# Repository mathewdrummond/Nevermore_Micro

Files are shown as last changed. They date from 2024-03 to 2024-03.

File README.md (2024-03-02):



# Nevermore Activated Carbon Filters - Micro Edition

<div align="center">Nevermore Micro V5 Duo (dual fan)</div>

Nevermore Activated Carbon Filter Micro V5 Duo

<div align="center">Nevermore Micro V4 (single fan)</div>

Nevermore Activated Carbon Filter Micro V4

Originally intended as a carbon fume filter for Voron V2, it has found its way into a multitude of other machines. Let yours be the next! Bad smells or fumes, or complaints thereof, should not keep you from being a maker!

- [Nevermore Activated Carbon Filters - Micro Edition](#nevermore-activated-carbon-filters---micro-edition)
- [About The Nevermore Micro](#about-the-nevermore-micro)
  - [Why The Nevermore?](#why-the-nevermore)
  - [Nevermore Background](#nevermore-background)
  - [Nevermore V4, First Release](#nevermore-v4-first-release)
  - [Nevermore V5 Duo](#nevermore-v5-duo)
- [FAQs](#faqs)
  - [What are differences between V4 and V5 Duo?](#what-are-differences-between-v4-and-v5-duo)
  - [Why use a single fan version, if dual is better?](#why-use-a-single-fan-version-if-dual-is-better)
  - [What other changes does V5 bring?](#what-other-changes-does-v5-bring)
  - [What fans should I use?](#what-fans-should-i-use)
  - [How do I make a suggestion/report a bug/find out more?](#how-do-i-make-a-suggestionreport-a-bugfind-out-more)
- [Getting Started](#getting-started)
  - [SOURCING THE PROPER ACID-FREE CARBON](#sourcing-the-proper-acid-free-carbon)
  - [NEVERMORE 3D PRINTER CARBON](#nevermore-3d-printer-carbon)
  - [BOM (V5)](#bom-v5)
  - [BOM (V4)](#bom-v4)
  - [Assembly](#assembly)
    - [Instructions for V5](#instructions-for-v5)
    - [Instructions for V4](#instructions-for-v4)
  - [Final Thoughts on Usage](#final-thoughts-on-usage)
- [Credits](#credits)
  - [Contributing](#contributing)
  - [License](#license)
  - [Contact](#contact)
  - [Acknowledgements](#acknowledgements)
  - [Special Thanks](#special-thanks)

# About The Nevermore Micro

[VOCs (Volatile Organic Compounds)](https://en.wikipedia.org/wiki/Volatile_organic_compound) are common in daily life but VOCs generated from 3D printing are known to cause severe health issues and even cause cancer in some cases.

Emitted VOCs

A study from 2013 of [ultrafine particle emissions from desktop 3D printers (2013)](https://www.sciencedirect.com/science/article/pii/S1352231013005086) is a good start to understand the importance of your filament choices and the printer's environment.

Characterization of volatile organic compound emissions from consumer level material extrusion 3D printers (2019)
_(credit: [Characterization of volatile organic compound emissions from consumer level material extrusion 3D printers (2019)](https://www.sciencedirect.com/science/article/pii/S0360132319304196))_

Characterization of particulate and gaseous pollutants emitted during operation of a desktop 3D printer (2019)
_(credit: [Characterization of particulate and gaseous pollutants emitted during operation of a desktop 3D printer (2019)](https://www.sciencedirect.com/science/article/pii/S0160412018323663))_

## Why The Nevermore?

At the end of the day, a fresh single-pass filtered exhaust (at brand new) has perhaps 70% VOC removal efficiency while still exhausting 30% of the nasty. A worn-in 50% efficiency recirculation filter achieving four passes would still remove 94% of the bad stuff. Or 99% at six passes!

The number of passes you get all depends on how well you can seal your build chamber.

Some will have a hard time achieving a good chamber seal, which creates the biggest drawback of recirculation filters - _they're air flow neutral_. Meaning, as nothing pulls air into the chamber, air can diffuse freely to the outside through any remaining gaps. And that air could be _zero-per-cent_ cleaned...

If you plan on using only a Nevermore - be sure to seal your chamber as good as possible to prevent diffusing.

## Nevermore Background

There are many options for 3d printing air filters. Here’s a short list, and why I eventually settled on creating Nevermore:

**1. Home air purifiers**

**PRO:** Plug and play! High air flow (mostly). Will filter most particles a 3d printer produces.

**CON:** ABS headaches are not from particles, but Volatile Organic Compounds (VOCs), that are two orders of magnitude smaller than any particles a HEPA or ULPA could trap - they’re essentially gasses.

While home purifiers typically also contains carbon filtration and/or photocatlytic UV filtration stages, they will still not be suitable for 3d printing. Why? Efficient carbon adsorption in sufficient amount and stages is an absolute airflow killer, so most purifiers contain only a thin layer of carbon mesh/pellets that will be fully adsorbed within days or weeks at full power. And even if the filter is not used, contact with air saturates the carbon in 1-2 months. Yet they’re advertised as lasting for 6 months – that's only true for the HEPA component, not the VOC adsorbant carbon we're after.

And replacement filters typically run 20-60 USD a pop. Quite a lot for changing every few weeks when the carbon component depletes.

UV photocatalyst activity can last though; however, breakdown is slow and inefficient with voc halflives of several hours. The TiO2 layer reacting to the UV will also easily get irreversibly blocked by silicates (of which there are a lot in peoples homes, in everything from sink and bathroom sealants to plaster walls). And breakdown will many times be incomplete. Styrene passing a PCO filter might get turned to even more dangerous benzene, for instance.

**2. Carbon/HEPA filter combinations like the Zortrax M Series HEPA Filters**

Same as above. The HEPA component will keep working, but the carbon is just a few pebbles per hex. It could provide partial VOC clearance when fresh, but will quickly deplete with air flow. Then you need to replace it for 36 USD after a week of printing.

**3. Wet scrubber**

Awesome for both particles and VOCs, but its an industrial solution with any smaller home versions plagued by loud noise, water leakage and mechanical issues. It's not a solution for the masses.

**So, how about Nevermore?**

Well, the carbon in those filters mentioned above, costing a lot for little duration is actually dirt cheap. Whereas you get 20 grams for 36 USD with a zortax filter, **you can get 5000 grams for 36 USD in bulk**.

And with an enclosed chamber, you don't need the air flow of a room-size air purifier. Even a 350mm V2 Voron only holds about 5cf, meaning even a partial flow from a 5015 fan of 0.5-2cfm is enough to filter the fumes efficiently at the source.

So what are we waiting for? We got lots of cheap carbon. We can replace it easily. We don't need high airflow to clean a small chamber. We deal with poor efficiency of one-pass carbon filters by multiplying the amount and recirculate the air.

Enter, _The Nevermore_.

## Nevermore V4, First Release

Nevermore V4 is a refinement of the V3. V4 adds a air guides, as the previous versions had the majority of air flow on just one side of the filter (most recent version has all supports removed yet again!). The cartridge lid also mounts a bit sturdier, and V4 now has separate base pieces for use with Vorons other than 2.4.

Nevermore Micro V2 Prototype

The V4 was the first official release of the Nevermore Micro to the public.

## Nevermore V5 Duo

Following the V4, the V5 Duo was released that changes the direction of air flow, better suited for when the Nevermore Micro would be placed flat on the bottom or top of the printer. Though there are other "outlet" options, like for the V1.8/Trident style that blows outwards and not up.

The V5 Duo also adds a 2nd additional 5015.

Nevermore Micro V5 Duo

Nevermore Micro V5 Duo

_(Nevermore V5 Duo. used with permission from Tightwad(JT)#6055)_

This repository hosts both versions, as they are the same in design and function.

# FAQs

## What are differences between V4 and V5 Duo?

The current NM Micro versions are V4 and V5 Duo.

V4 utilizes a single dissected 5015 fan that is glued in place to spread the airflow over the entire filter surface (something impossible to do with an intact scroll, which focuses the air too much). The intake is on the top, and exhausts out the front.

V5 Duo uses two blowers in parallel to achieve a more even spread of airflow while keeping the pressure-generating scrolls intact; however, it still needs some slight modifications to the scroll exhaust. The intake is on the top, and exhausts upwards.

## Why use a single fan version, if dual is better?

_Dual is not better._ The area per blower is halved, so what is gained in air flow is lost in increased restriction per blower. There should be some improvements though, from linear air flow and intact scroll.

Also, the V4 single fan version may be better suited for printers where the Micro has to be mounted vertically, like on the side of a Voron V0.

Voron V0.1 with Nevermore V4

_(Voron V0.1 w/Nevermore V4. used with permission from DoubleT#0448)_

The single fan version of the V4 design in the Voron V0 above would draw the air from under the build plate, and exhaust it upwards, creating a circulation flow within the printer.

Air circulation is critical to filter as much of the VOCs within the build chamber as possible. Not only that, but it would help heat the chamber faster and achieve higher chamber temps.

However, on a Voron V2 or similar printer, the V5 Duo version would be better suited when placed under the bed as the upward exhaust venting creates a good circulation effect.



_(Voron V2 w/Nevermore V5. used with permission from Laserbeak43#2729)_

## What other changes does V5 bring?

- Exhausts air upwards
  - Better heat spread in the Voron V2 chamber
  - Less air leaks through Voron V2 split doors
- BOM 6x3 magnets are standard
- Blower fans are seated by bolts again, with less modifications needed

## What fans should I use?

Aim for any 5015 blower with a rating above 200Pa / 20mmH2O / 1 inH2O.

Since the fan (probably) cant be reused for other projects and will function in a high temp environment affecting its lifetime, go for budget. The Sunon Maglev MF50151VX (12V) / MF50152VX (24V) (high speed version, 6000 rpm) is good but unfortunately almost impossible to find as most are fakes. The GDStime 6000rpm Dual Ball bearing is another good option, but quality may vary. The Delta BFB0524HH is a gucci option, as is the special micro versions made for the papst rlf-35 which is an equally awesome and expensive fan. Any fan that works well for stealthburner should be a good option for nevermore micro as well.

See the BOM below for more details.

## How do I make a suggestion/report a bug/find out more?

- [The Nevermore Micro](https://github.com/nevermore3d/Nevermore_Micro)
  - [Report a Bug](https://github.com/nevermore3d/Nevermore_Micro/issues)
  - [Request a Feature](https://github.com/nevermore3d/Nevermore_Micro/issues)
- [Explore all Nevermore Activated Carbon Filters](https://github.com/nevermore3d)

# Getting Started

You're ready to build a Nevermore Micro? Cool!

> [!NOTE]  
> MADE FOR ABS/PC/PETG - USE A DECENTLY HEAT RESISTANT FILAMENT !!

> [!NOTE]  
>  Since you are committing to fan dissection, be aware a 5015 used for a NM Micro will most likely never find a different purpose!

## SOURCING THE PROPER ACID-FREE CARBON

**IMPORTANT!** Since first release the varying quality carbon out there has become increasingly evident. Users has both gotten bad carbon as well as outright dangerous stuff (in one case oxidizing most metal surfaces in a new voron in minutes. Be sure to vet your carbon supplier! You do not want your printer to look like this.

Acid residue on end-stop switch oxidizing

_(z end-stop switch after using acid residue carbon for 30 minutes, oxidizing)_

Acid residue on rails and screws oxidizing

_(oxidation on rails and screws after using acid residue carbon. used with permission from Zeptron#8880)_

Acid residue on filament tension spring oxidizing

_(oxidation on filament tension spring after using acid residue carbon. used with permission from Zeptron#8880)_

Acid residue on bolts and washers oxidizing

_(oxidation on bolts and washers after using acid residue carbon. used with permission from Zeptron#8880)_

Optimal carbon for 3D printer VOC adsorption is sourced from **virgin coconut**, not wood/bitumen/charcoal/bamboo/lignin/etc. The porosity for each and every source will vary greatly.

For example, for aquarium or moonshine use you want large macroporosity to filter larger impurities, like oils. For that reason, water/liquid-use carbon has a large macropore area, defined as >100nm. 3D Printer VOCs are generally less than 0.5 nm, meaning that **for optimal capture rate and efficiency we want carbon with a high microporosity ratio, defined as <1nm**. A higher iodine count >1000 usually indicates at least some micro/mesoporosity, and a higher hardness (>95%) will create less dust in air filtration. CTC number doesn't translate well to our VOCs; however, toluene adsorption - which sometimes is available - is a good metric.

**Avoid acid washed carbon at all costs**. Residues have oxidized printers! Go for steam activated, non acid-washed. A blend of neutral carbon and alkaline KOH carbon might be the best blend in the future, but impossible to currently source from trustworthy manufacturers.

Finding carbon that fills all criteria is hard. Look around, ask suppliers about the carbon, hear what others recommend. 

## NEVERMORE 3D PRINTER CARBON
**Nevermore offers its own premium carbon of unmatched specifications through selected voron resellers.** Its the best activated carbon for 3D printer use we have found after speaking to most major, vetted suppliers, offering benzene adsorbtion of up to 48 wt%, surface area of 1250 and CTC value of 80. It doesn't come cheap compared to bulk carbon from amazon, but its safe, has unbeatable performance, and every purchase supports the nevermore project by at least a dollar.  

[All Nevermore resellers here](https://github.com/nevermore3d/Reseller)

## BOM (V5)

- 2x 5015 blowers (rating above 200Pa / 20mmH2O / 1 inH2O)
  - Sunon Maglev MF5015VX (high speed version, 6000 rpm. NOTE: There are A LOT of fake sunons out there, even from usually reputable sources. Blantant examples include 24V versions. Also, Sunon does not officially reecommend PWM:ing this fan, so while its still perfectly doable it can have unintended consequences later on) (There is no 24V version for this fan only comes in 12 V)
  - GDStime 6000rpm Dual Ball bearing on Aliexpress (This is 12V rated fans)
  - Delta BFB0524HH (This is 24V rated fans)
  - Avoid mechatronics fans for this purpose.
- 6x M3, 5 mm OD, 4 mm height heatset inserts (standard voron issue)
  - 1 in plenum base to secure plenum lid
  - 1 in cartridge base to secure cartridge lide
  - 4 in fans (2 in each fan × 2 fans)
- 8x ⌀6x3 mm round magnets
- 1x 2 pin JST header
- 4x M3x16 BHCS
  - for heat inserts that go into the four fan tabs
- 1x M3x18 BHCS
  - ONLY for delta and v1.8 variants
- 1x M3x6 BHCS
- 1x M3x4 BHCS
  - for the extra hole in the plenum@lid for symmetry (it doesn’t attach to anything and is totally optional)

Acid-free Activated Carbon

- 4mm Active Carbon Air Filter Pellets

Optional for the cartridge closure

- 1x M3x0.5mm Heatset inserts
- 1x M3x6 BHCS

Optional for Vorons or any printer with 2020 extrusions

- 2x M3x12 SHCS
- 2x M3 2020 T-Nuts

Optional for Vorons or any printer using 24PSU
- 24 to 12 buck converter

## BOM (V4)

- 1x 5015 blowers (rating above 200Pa / 20mmH2O / 1 inH2O)
  - Sunon Maglev MF5015VX (high speed version, 6000 rpm. The 5000 rpm might be okay also)
  - or, the $4-6 GDStime 6000rpm Dual Ball bearing on Aliexpress
- 4x M3, 5mm OD, 4mm height Heatset inserts (standard voron issue)
  - 2 for seating plenum to base
  - 2 for seating plenum lid to plenum
- 8x ⌀4x6 mm or ⌀6x3 mm magnets
  - Make sure to print correct parts (4x6 or 6x3 files)
- 1x 2 pin JST header
- 2x M3x10 SHCS
  - for seating plenum to base
- 2x M3x6 BHCS (any size, fits up to 20mm)
  - for seating plenum lid to plenum

Acid-free Activated Carbon

- 4mm Active Carbon Air Filter Pellets

Optional for Vorons or any printer with 2020 extrusions

- 2x M3x12 SHCS
- 2x M3 2020 T-Nuts

## Assembly

Check out assembly images (**take note at how the fans are cut!**) here: [Nevermore V5 Plenum Assembly Album](https://ibb.co/album/0BN405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)

### Instructions for V5

Print pieces without supports. This goes for all Nevermore parts. Do note that there as **built-in support** below the cartridge insert. This is meant to be easily removed by pushing or crushing (it's a single line wall). 

### Instructions for V4

Start by cutting up the 5015 so just the center remains. Take off the top half, cut the bottom piece circular along the fan blades. We aim for removing the focused air stream and instead achieve an even pressure across all of the filter medium.

The Nevermore Micro has three main parts: **Base**, **Plenum**, and **Cartridge** (plus lids for the plenum/cartridge).

- **Base** is mounted in the 130mm space between the bottom extrusions found on many vorons (designed for v2 originally). It’s seated with one m3 on each side, that screws into to a receiving 2020 M3 T-nut.

- **Plenum** holds the cut up 5015 fan, and is seated with two m3 screws into the base (base has two recieving m3 4mm heat inserts) on each side.

- **Cartridge** holds the filter medium of your choice (made for 4mm air filter active carbon pellets, but feel free to filter with what you think works best!). It snaps onto the Plenum piece for easy and quick removal.

For wiring, you are free to connect however works with your printer. If you do not have any direct controls on your MCU (controller board), then directly wiring may be your only option (with an inline switch).

However, if your MCU does have an additional fan output, then it is recommended to connect to it. If you are using Klipper on a Raspberry Pi, you have the option of using PWM fans and connecting the control wire to one of your PWM outputs on the RPi 40-pin header.

## Final Thoughts on Usage

**PID tune AGAIN if a Nevermore Micro is installed right beneath a heated bed, or draws/exhausts air over the bed thermistor. This is important, as worst case it could cause the bed to overheat, and/or make the heater adhesive burn (this will smell worse than any ABS printing!), and/or possibly even damage the bed heater.**

The Nevermore Micro's activated carbon will not filter Ultra-Fine Particulates (UFP). This is what the HEPA filter does in the Nevermore Mini (not released yet) and [Nevermore Max](https://github.com/nevermore3d/Nevermore_Max) variants. Those also have built-in negative-pressure fans.

However, you can achieve the same results with the Nevermore Micro by using a HEPA filter of your own and creating slightly negative air-pressure within your build chamber, exhausting air outwards at a slow pace. Since you are filtering with the Nevermore, the vast majority of VOCs will be filters by the active carbon filtration, leaving the HEPA filter to capture the remaining UFPs. This also greatly extends the live of your HEPA filter as the Nevermore Micro will be accumulating the larger particulates.

To create a negative pressure within your build chamber, simply install a fan to slowly draw air out of your build chamber and our through a HEPA filter. Voron machines already have such a design with their rear exhaust housing for HEPA filters.

The negative pressure will also eliminate diffusion, especially if your build chamber is not completely sealed.

# Credits

The Nevermore Activated Carbon Filter was modelled in [Fusion 360](http://autodesk.com).

## Contributing

Please contribute! I'd like to incorporate VOC sensors, making the filter smart (running on low-noise mode at an acceptable VOC level, then ramp up at the end to clean more thoroughly before doors open).

## License

Distributed under GNU General Public License version 3.0 (GPLv3)

## Contact

- Discord: 0ndsk4 - (<https://discord.com/user/0ndsk4>)
- Nevermore: [https://github.com/nevermore3d](https://github.com/nevermore3d)

## Acknowledgements

- [The Voron Dev Team](https://vorondesign.com/)

## Special Thanks

- [eduncan911#4852](https://github.com/eduncan911) as the Git Guru to publish all of this

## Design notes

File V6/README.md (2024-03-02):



# Nevermore Micro V6

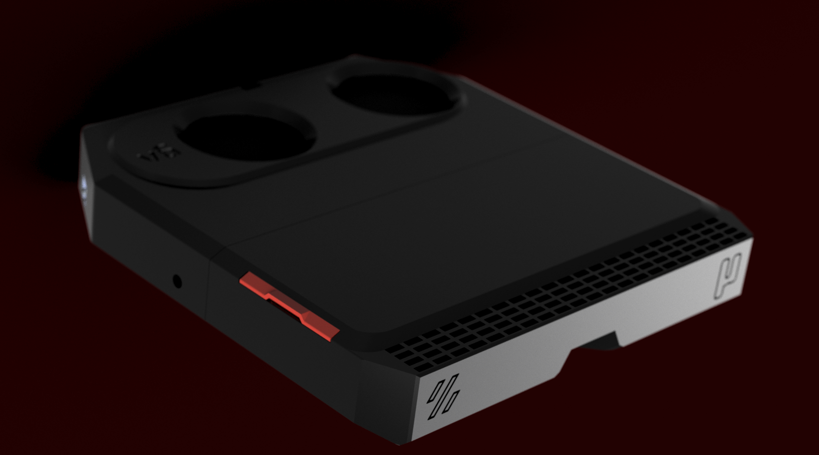
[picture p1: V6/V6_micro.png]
Nevermore Micro V6


Nevermore Micro V6 is here! It is designed to supersede both the V4 and V5 duos, which will soon be considered legacy designs.

## What's New?

- **Intact 5015 Fans:** V6 now make use of fully intact 5015 fans, eliminating the need to cut the fan scroll or wires. This raises a concern: does it waste carbon if airflow from a small 15mm 5015 fan exhaust isn't spread over the entire 130mm filter surface? Yes, usually - however, we have overcome this challenge through use of evasees and vanes to efficiently spread the airflow within the small plenum space. This means all the carbon receives airflow immediately, without requiring any fan modifications.

- **Enhanced Heat Tolerance:** Unlike its predecessors, V6 can tolerate higher levels of heat. The V4 and V5 had thinner lids that could bend or warp, especially when subjected to temperatures above 100°C under a heated bed. This sometimes resulted in broken or damaged units. However, the V6 is beefed up to address this issue. With a thicker frame, structured vanes, and lids strategically placed away from the heat source, the chances of melting a Nevermore Micro are significantly reduced.

- **Improved Airflow:** V6 boasts superior airflow. We have achieved this by optimizing the printing direction, which allows for built-in seals. Say goodbye to air leaks between the cartridge and the plenum! Furthermore, the air intakes have been redesigned to accommodate increased airflow. Now, it can process the chamber volume of a 250 Voron in just 30 seconds, and a larger 350 in approximately 2 minutes.

- **Reduced Noise:** V6 generates less noise compared to the V5, thanks to a redesigned air intake.

- **Compatibility:** V6 can be printed on any machine, including on a Voron v0 on which a v5 duo previously wouldnt fit. Yet the size is the same, its dark sorcery.

- **Sleek Design:** V6 not only performs exceptionally but also looks awesome. It features a novel jalousie lid design with no bolts, allowing for convenient one-handed carbon swaps. Gone are the days of dealing with annoying bolts or latches when swapping carbon. Rest assured, this design remains super secure. You have to try it to believe it! Jalousie demo [here](https://youtube.com/shorts/sSmVfhcDKrI?feature=share).

## Print material and settings
- Designed and prototyped with ABS materials. Any material that is heat resistant enough for the installation spot will likely work, but brittle material (i.e regular PLA) should be avoided for the jalousie slider and the spring fan fasteners.
- Made for standard voron settings. 0.2 mm layer height needed for supports to line up right, and 0.4-0.5mm line width for optimal mesh printing. 5 walls recommended for jalousie structural integrity, otherwise its pretty sturdy regardless.
- **JALOUSIE** can be break if your slicer settings interferes with the intended extrusion path. A suggestion from @Haldamir is to print it with 0 bottom solid, 1 top solid layers, 5 perimeters and 0.4 extrusion width. Also 90 degrees infill angle, so the 3rd layer is printed in this orientation.
**Avoid** bottom horizontal expansion so that there are no large gaps between the parallell length-wise extrusion lines (built in gaps in the bottom and second layer forces the slicer to print in a length-wise paralell pattern. Ideally, you want these gaps to fuse slightly for greatest strength).
  Some users has reported going **slow** for the first three layers improves the structural rigidity, as it gives more time for the layers to fully fuse. If your jalousie is prone to crack, try slowing down to 40mm/s and perhaps raise the **temp** slightly for better fusing. There is also a "thin" jalousie that might be a better fit for stiffer materials. It has bend layers that are 0.4mm instead of 0.6mm, which paradoxically will make a jalousie prone to cracking with _bending_ hold up better.

## BOM and Installation

### Support Removal

Before installation, there are a few support pieces that need to be removed:

**Plenum:**
- A long bridge along the top of the cartridge.
- The two triangular pillars extending to the fan tab slot from the area around the fan intakes.
- The top portion of the two fan intakes.
- On the bottom right evasee/side bolt mount slot as viewed from the front.

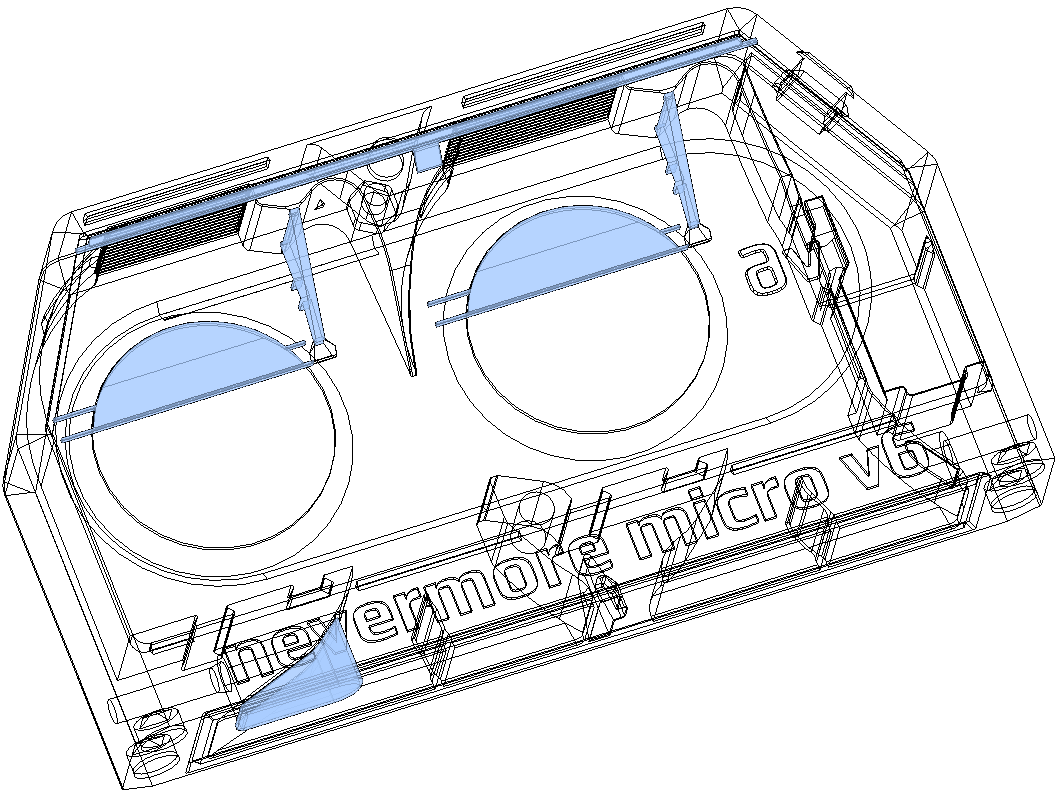
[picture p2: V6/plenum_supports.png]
Plenum Supports


**Cartridge:**
- The lid/jalousie area has a single support piece. Be cautious when removing it, ensuring not to damage the jalousie sliding path. If the support is fused, use an X-Acto knife if necessary.

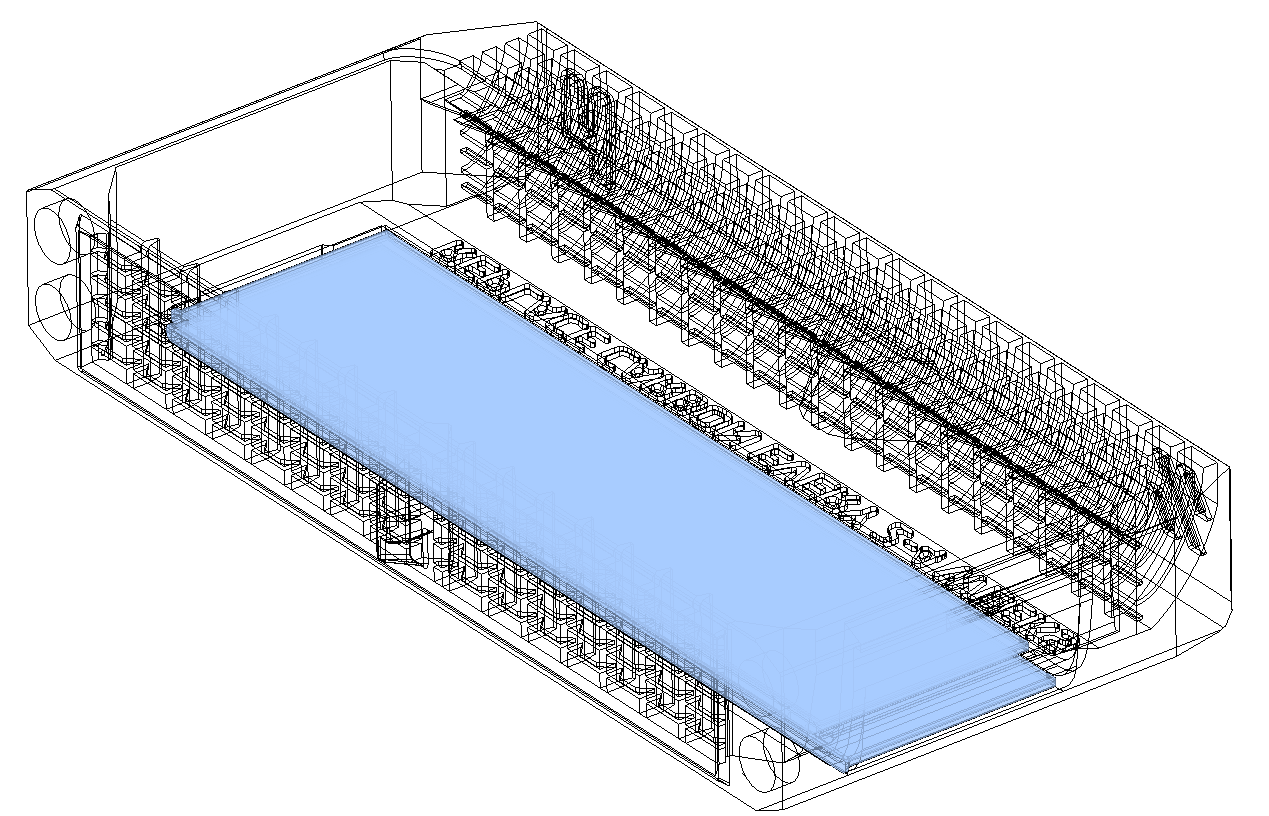
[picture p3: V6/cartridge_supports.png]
Cartridge Supports


### Plenum

#### Electronics

**Required:**
- 2x 5015 blowers (compatible with Delta, Honeybadger, Gdstime, and Winsin. Sunons might fit but the intake holes may not line up perfectly). It is recommended to use blowers with good static pressure (>150Pa).

**Wiring Options:**
1. **Single JST-XH 2-pin**: Solder both fan wires to a single JST-XH 2-pin connector and connect it to the plenum port.
2. **Triple JST-XH 2-pin**: Print the [2xJST_Holder.stl] insert to create a triple JST-XH 2-pin port. Connect the fans without cutting fan wires by daisy-chaining the 2 extra JST connectors to the plenum JST port. Note that for thicker and longer fan wires (like Gdstime), the wiring space may need to be completely filled with wire.
3. **Dual WAGO 221 2-pin connectors**: Cut the fan wires, twist the fan wires together (12V bundle + GND bundle), and use WAGO connectors (One WAGO for 12v bundle, and another WAGO for GND bundle) as wire extensions. Print the [Wire_connector.stl] that fits the plenum JST port. Insert the power wire from your printer and connect it to the corresponding WAGO socket. Lastly, insert the WAGO connectors into their slots.

**TRIPLE-JST and WAGO**
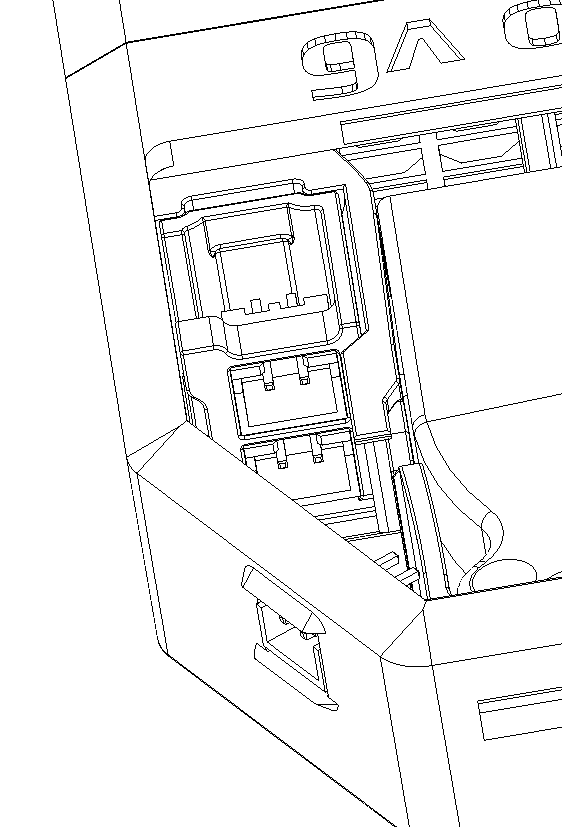
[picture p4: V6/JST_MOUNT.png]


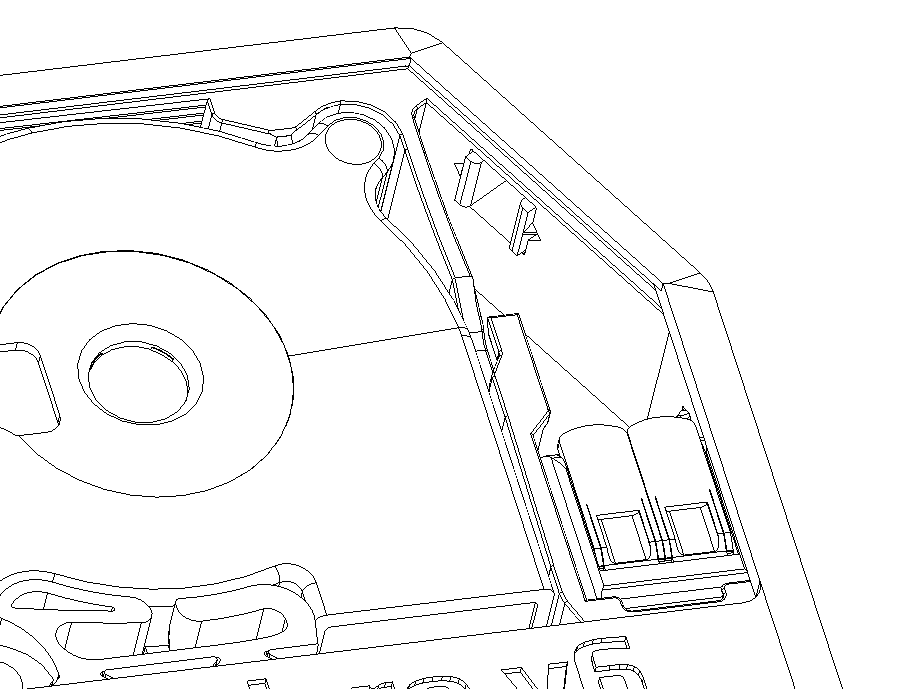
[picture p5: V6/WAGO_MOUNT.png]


#### Magnets

**Required:**
- 4x 6mm wide and 3mm deep magnets (also 4x magnets on the cartridge side, totaling 8 magnets).
**Note:** Take care when installing the magnets. A common issue is getting polarity wrong.

### Plenum Wiring and Lid Install

Plenum_Install
Plenum_Install

#### Back Extrusion Mounting

For the V0 1515 version or Trident 2020 version:
- Insert 2x M3x4x5 heat inserts, one in the back slot after lid installation, and one to secure the lid fully after snap fitting it.
- Use an extrusion T-nut.
- Seat [2020_Frame_Connector.stl] _OR_ [1515_Frame_Connector.stl] into the extrusion T-nut with an M3x6mm SHCS.
- Slide the plenum over the extrusion connector and connect the pieces with one M3x16 SHCS from the front side of the plenum.

#### Bed Extrusion Mounting

For the V2 2020 version (or sometimes the Trident 2020 bracket):
- Insert 1x M3x4x5 heat inserts, to secure the lid fully after snap fitting it (or both inserts as per above if you plan on using one back, and one side mount)
- 2x extrusion T-nuts.
- 1x m3x16 SHCS (left side mount when viewed from top/exhaust)
- 1x m3x20 SHCS (right side mount mwhen viewed from top/exhaust)
- Bolt the V6 to an extrusion t-nut on both side of the filter when mounting under the bed on a v2. 
**Note:** Bed doesnt have to be removed; connect the wires and bolt the plenum at the front of the bed, then loosen the bolts by half a turn allowing you to slide it in to position. Once in the right position, tighten it gently with a ball type driver.

### Cartridge

#### Magnets

**Required:**
- 4x 6mm wide and 3mm deep magnets (also 4x magnets on the plenum side, totaling 8 magnets).

#### Jalousie Sliding Lid Installation

The jalousie slider can be printed in any non-brittle yet rigid material. ABS, ABS+, Nylons, PETG, and Tough PLA are suitable options. However, avoid using brittle PLA or TPU.

For the first installation, **heat the jalousie slider slightly** (for instance, by placing it on the 3D printer's heated bed just below the glass transition temperature for a minute or two). Then, insert it from the top, ensuring the matching orientation, and push it in a few millimeters at a time. The critical moment is the first bend on the first insert, so **provide support and help it bend on the opposite side of insertion to prevent cracking or damaging the sliding path**. Once inserted, slide it in and out a few times to smooth out any surface imperfections that may hinder smooth operation. Lubrication should not be necessary but can be an option if desired.

## Support My Work

If you find my work helpful, consider [buying me some filament 🖍️](https://www.buymeacoffee.com/nevermore3d).
## For more information and documentation, visit our [GitHub page](https://github.com/nevermore3d).

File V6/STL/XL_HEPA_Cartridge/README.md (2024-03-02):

# Nevermore Micro - XL?!
This cartridge is double the thickness of a regular cartridge, and wont fit under a voron v2 bed. It does however fit along a panel on any machine with at least 42 mm of space between the panel and bed. The extra height allows the installation of a Xiaomi Mijia G1 [HEPA filter](https://s.click.aliexpress.com/e/_EGPsFBt) (same as on Nevermore Stealthmax), of the size 130x40x8mm.
<div align="center">Nevermore Micro V6 XL HEPA</div>

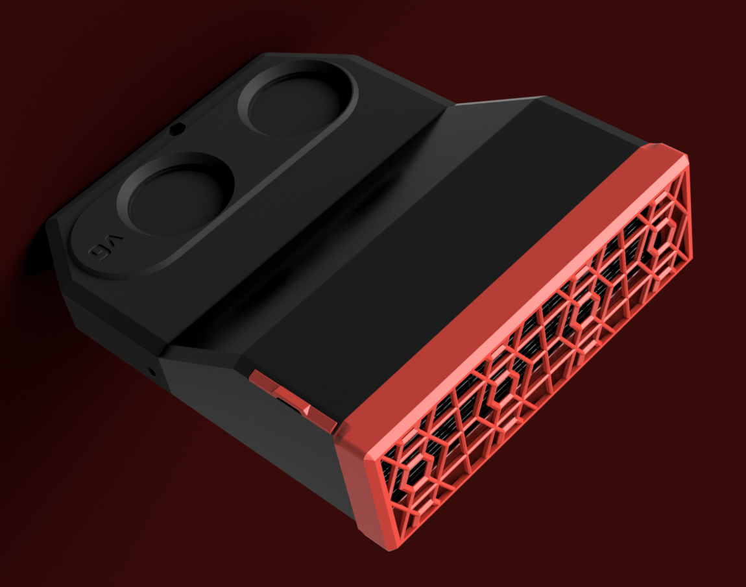
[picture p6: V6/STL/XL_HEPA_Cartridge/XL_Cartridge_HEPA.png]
Nevermore Activated Carbon Filter Micro V5 Duo Nevermore Activated Carbon Filter Micro V6


<div align="center">Nevermore Micro V6 XL HEPA</div>

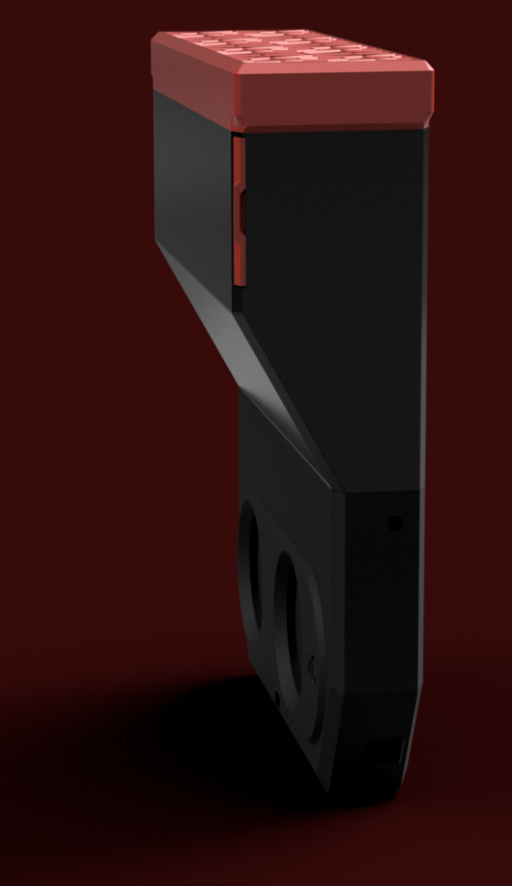
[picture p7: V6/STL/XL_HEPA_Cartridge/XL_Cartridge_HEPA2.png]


<div align="center">Nevermore Micro V6 XL HEPA</div>

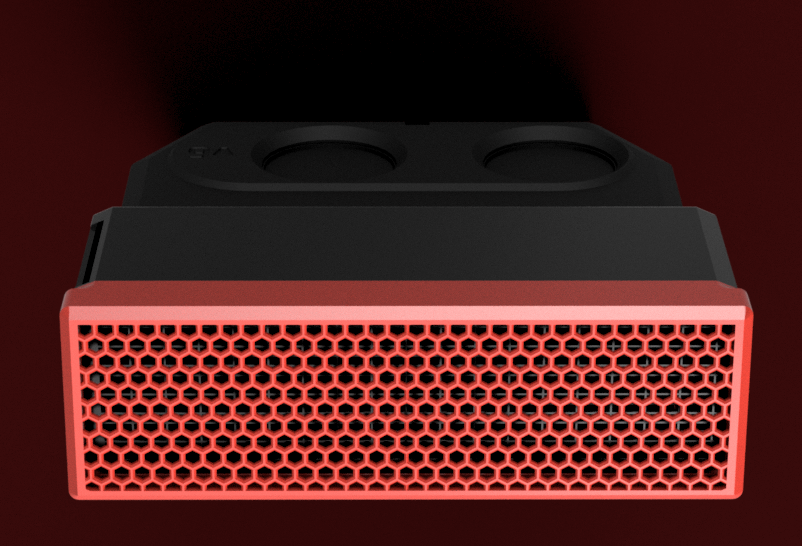
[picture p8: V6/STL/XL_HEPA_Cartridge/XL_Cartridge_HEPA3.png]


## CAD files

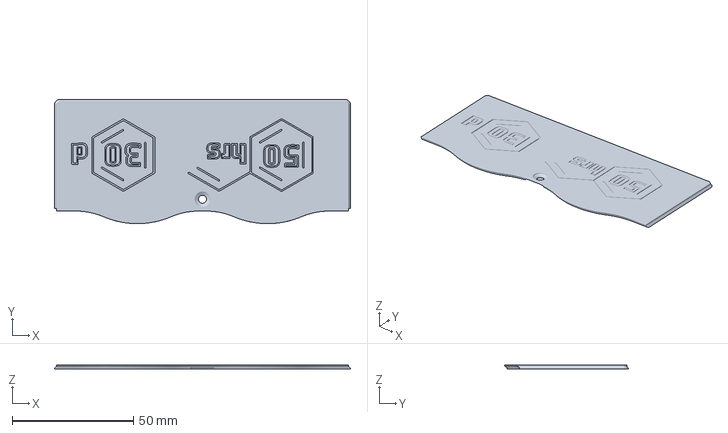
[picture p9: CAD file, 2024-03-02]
V5_Duo/V2/Regular_Cartridge_Lid(contributed_by_Bucknova).3mf
122.0 x 51.2 x 1.78 mm

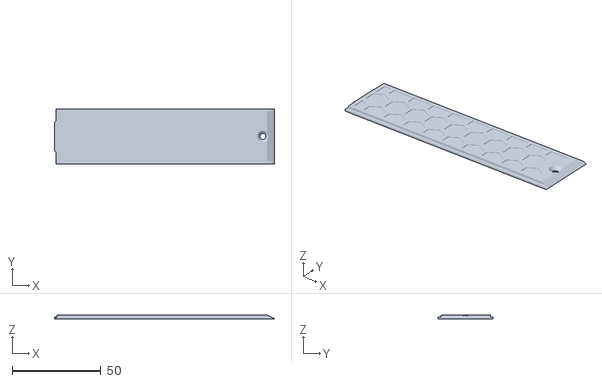
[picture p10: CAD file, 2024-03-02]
V6/STL/Alternate_Cartridge_door_Mod/Sliding_door.stl
124.0 x 31.2 x 2.20

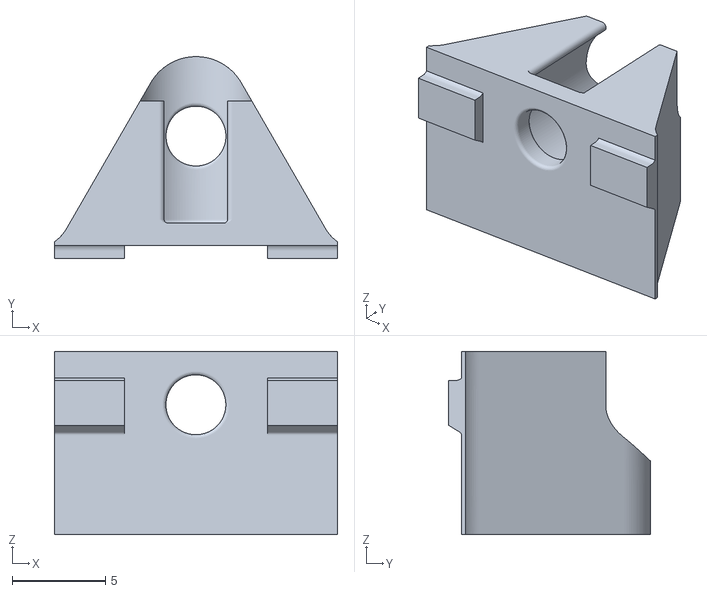
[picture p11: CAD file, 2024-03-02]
V6/STL/Optional_stuff/1515_Frame_Connector.stl
15.1 x 10.8 x 9.79

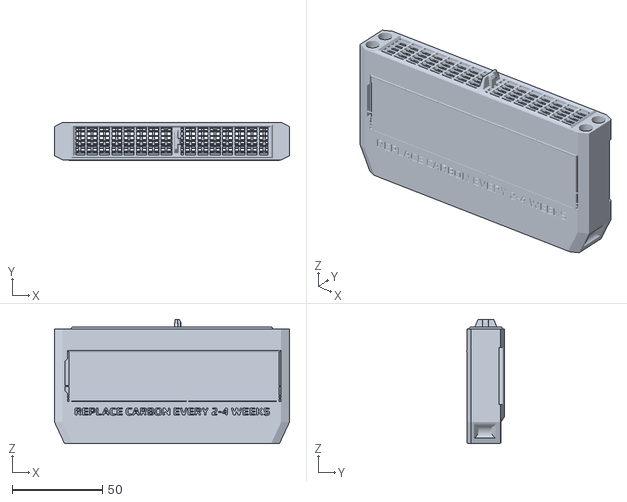
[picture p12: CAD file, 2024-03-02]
V6/STL/v6_Cartridge_Straight.stl
130.0 x 21.0 x 68.7

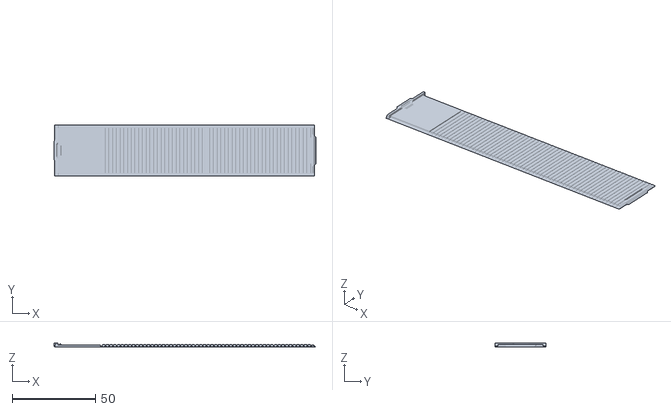
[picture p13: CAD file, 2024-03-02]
V6/STL/XL_HEPA_Cartridge/3_XL_Jalousie[stiff_filament].stl
157.7 x 30.8 x 2.66

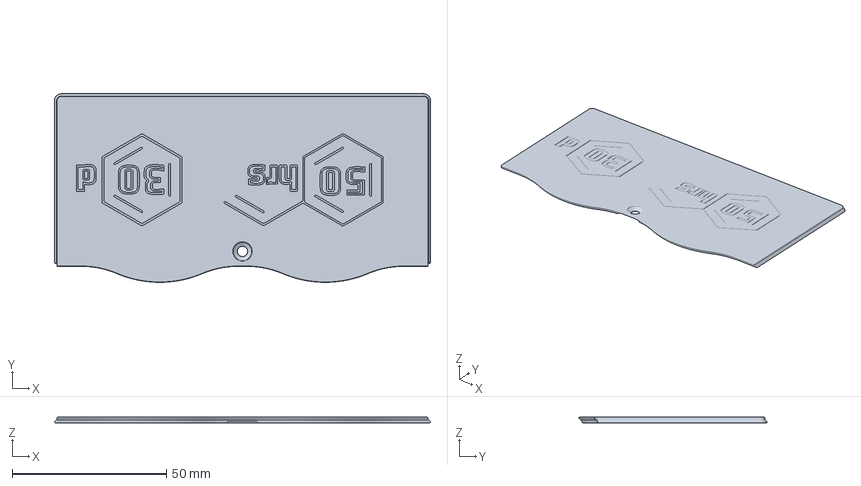
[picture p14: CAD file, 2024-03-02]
V5_Duo/V2/XL_Cartridge_Lid(contributed_by_Bucknova).3mf
122.0 x 61.2 x 1.78 mm

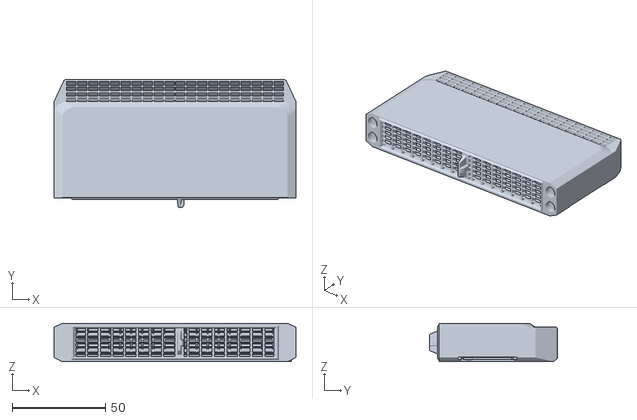
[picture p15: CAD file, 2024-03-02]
V6/STL/Alternate_Cartridge_door_Mod/v6_Cartridge_90deg_Sliding_Door_Mod.stl
130.0 x 68.7 x 20.6

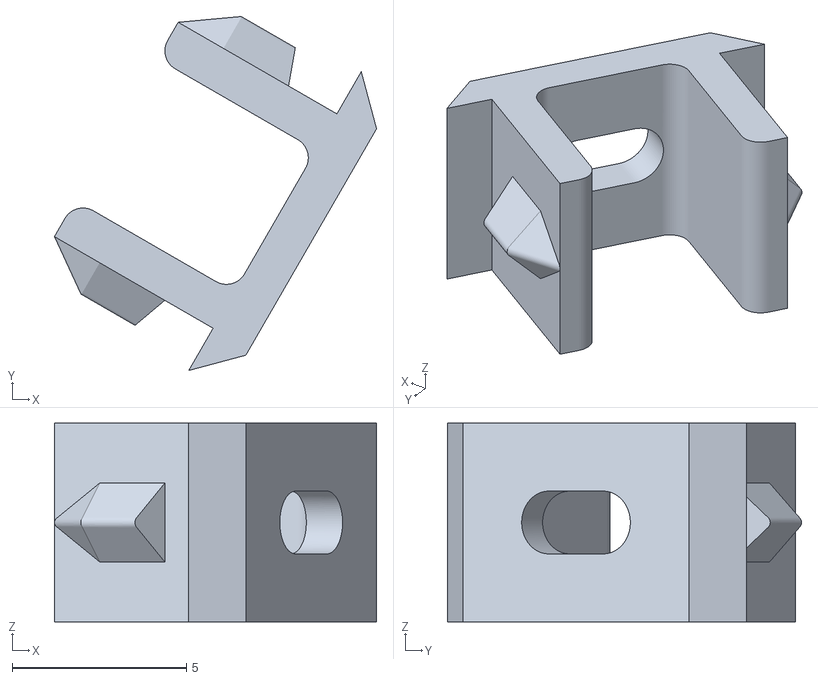
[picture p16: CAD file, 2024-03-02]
V6/STL/Optional_stuff/Wire_connector.stl
9.24 x 10.2 x 5.70

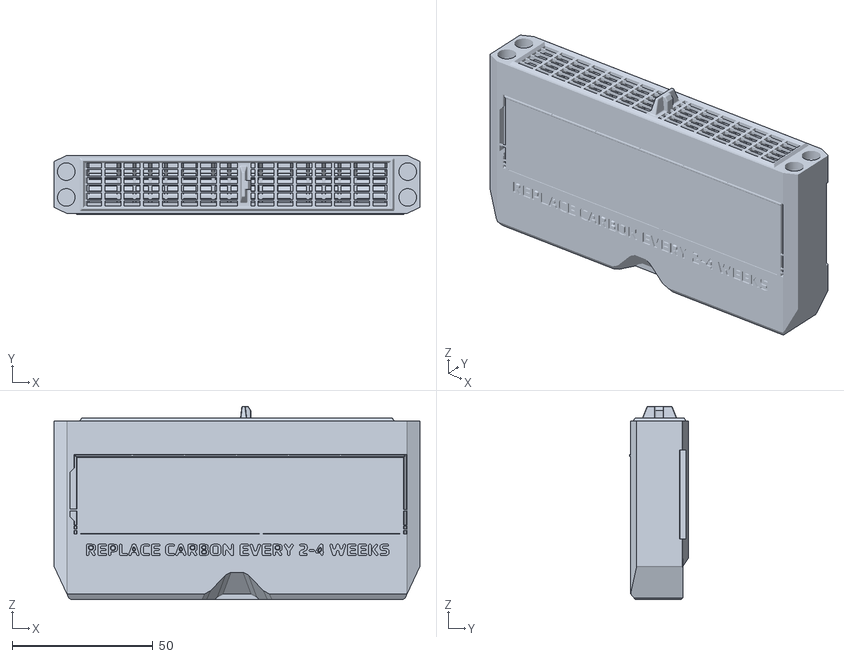
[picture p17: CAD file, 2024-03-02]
V6/STL/v6_Cartridge_90deg.stl
130.0 x 21.0 x 68.7

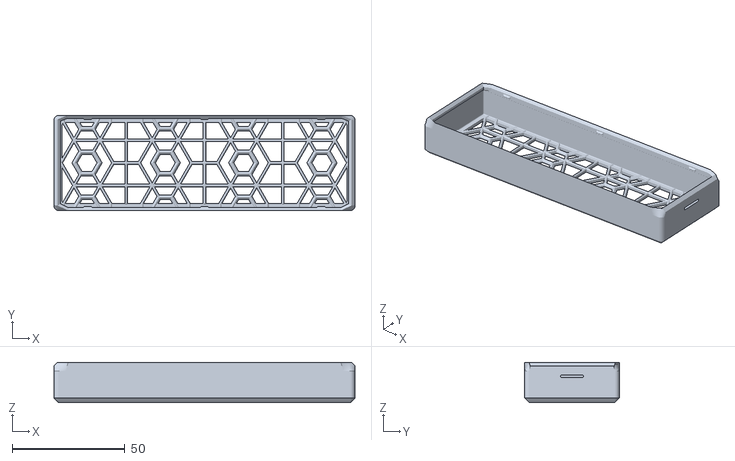
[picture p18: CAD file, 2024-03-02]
V6/STL/XL_HEPA_Cartridge/2_XL_HEPA_Container[reg].stl
133.2 x 42.0 x 17.7

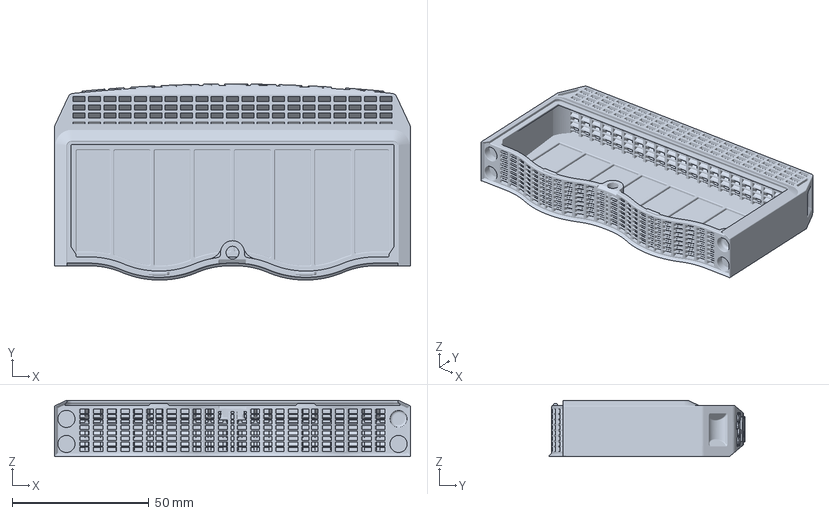
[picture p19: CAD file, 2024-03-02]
V5_Duo/V2/Regular_Cartridge(contributed_by_Bucknova).3mf
130.0 x 71.6 x 20.5 mm

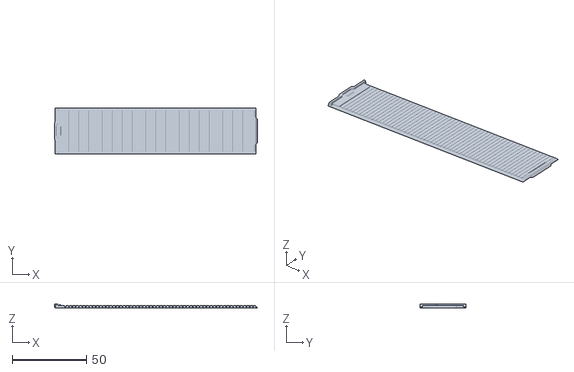
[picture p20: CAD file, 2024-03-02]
V6/STL/[a]V6_Jalousie_Slicer.stl
136.4 x 30.8 x 2.86

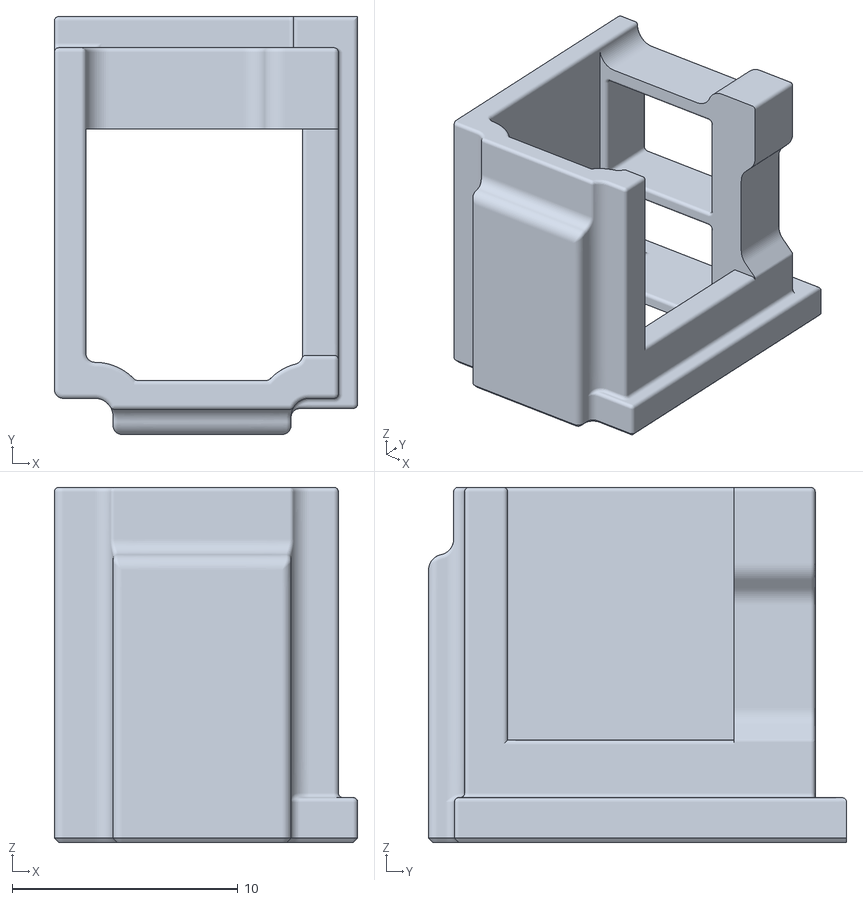
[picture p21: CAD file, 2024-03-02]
V6/STL/Optional_stuff/2xJST_Holder[no_cut_fan_wires].stl
13.4 x 18.5 x 15.8

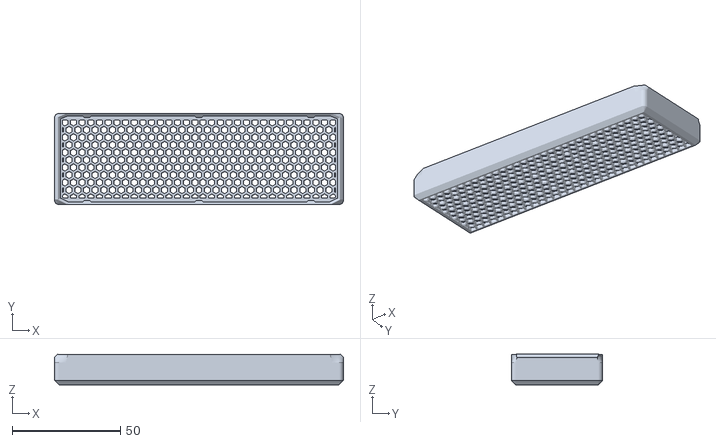
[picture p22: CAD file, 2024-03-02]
V6/STL/XL_HEPA_Cartridge/2_XL_HEPA_Container[small_hex].stl
133.2 x 42.0 x 14.1

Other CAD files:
V6/v0/v0_Straight_Cartridge.stl
V6/v0/v0_90deg_Cartridge.stl
V5_Duo/V2/XL_Cartridge(contributed_by_Bucknova).3mf
V6/STL/[a]V6_Jalousie_Slicer_THIN[Stiff_filament][7_walls].3mf
V5_Duo/V0/V0_Plenum.f3d
V6/Jalousie_ v2.f3d
V6/STL/Optional_stuff/2020_Frame_Connector.stl
V6/STL/Optional_stuff/v6_trident_rear_mount.stl
V6/STL/V6_Plenum_Lid.stl
V6/STL/XL_HEPA_Cartridge/1_XL_Cartridge.stl
V6/STL/XL_HEPA_Cartridge/3_XL_Jalousie[ABS_plus_or_softer].stl
V6/STL/XL_HEPA_Cartridge/3_XL_Jalousie[THIN_with_PULLTAB].stl
V6/STL/[a]V6_Jalousie_Slicer[TAB][THIN].stl
V6/Sunon_Honeybadger_FAN/V6_PLENUM_1515_SUNON_HONEYBADGER.f3d
V6/Sunon_Honeybadger_FAN/V6_PLENUM_2020_SUNON_HONEYBADGER.f3d
V6/V6_90_Degree_Cartridge.f3d
V6/V6_PLENUM_1515_Extrusion.f3d
V6/V6_PLENUM_2020_Extrusion.f3d
V6/v0/V0_90_Degree_Cartridge_V6.f3d
V6/v0/V0_PLENUM_1515_Extrusion_V6.f3d
V6/v0/V0_PLENUM_1515_SUNON_HONEYBADGER_V6.f3d
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

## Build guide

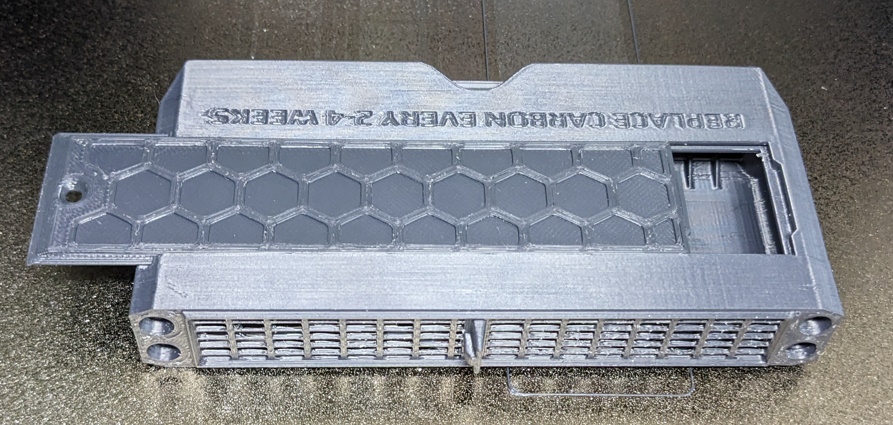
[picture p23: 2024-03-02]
V6/STL/Alternate_Cartridge_door_Mod/After_Printing.jpg
